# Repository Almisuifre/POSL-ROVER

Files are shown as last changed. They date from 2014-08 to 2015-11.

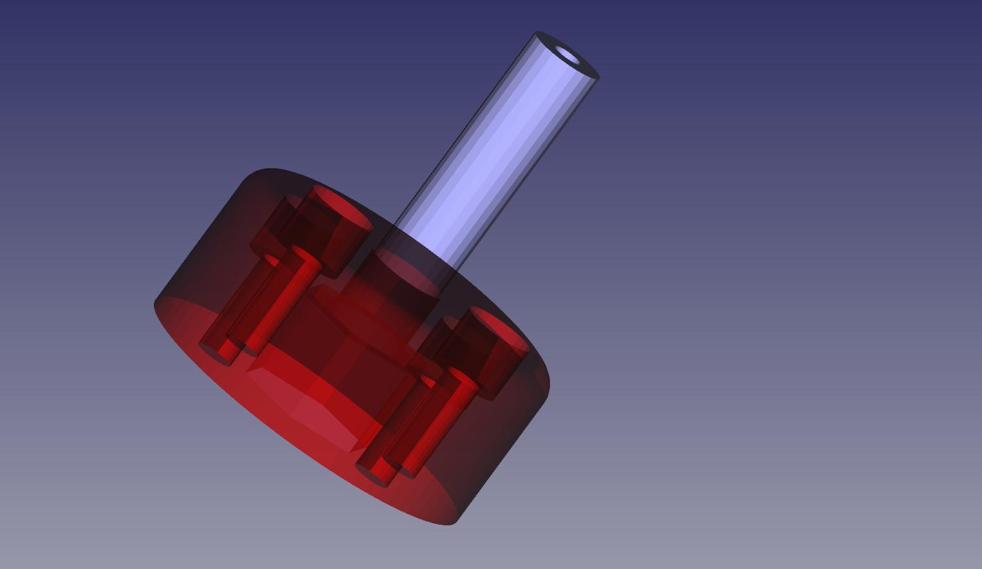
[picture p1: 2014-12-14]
Images/Assemblage-Chapot-pivot-et-pivot-axe.jpeg

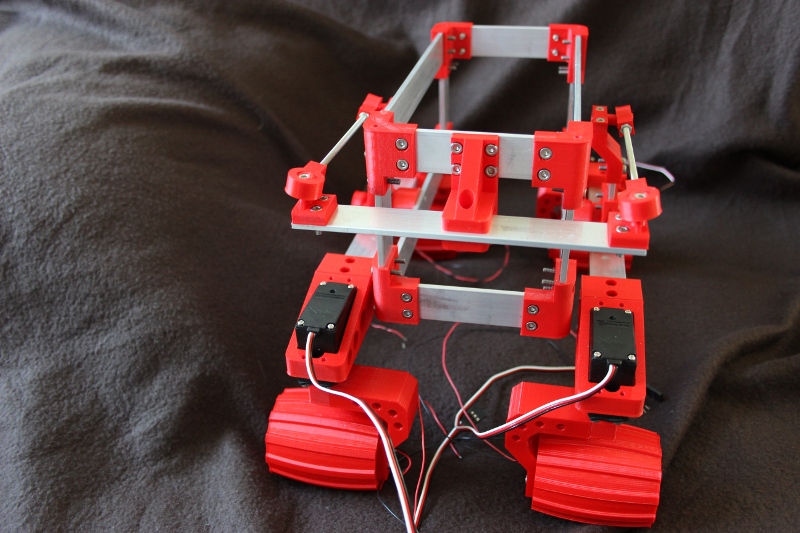
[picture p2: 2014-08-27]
Galerie/Montage-1/Img_002.jpg

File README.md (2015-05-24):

POSL

INFORMATIONS GENERALES
-----------------------------------------------------
-POSL est l'acronyme de Projet Open Source et Libre.

-L'ensemble du projet repose entièrement sur des logiciels Open Source et son hébergement est sous GitHub.

-----------------------------------------------------

LICENCE
-----------------------------------------------------
POSL Rover de Almisuifre est mis à disposition selon les termes de la licence Creative Commons Attribution - Partage dans les Mêmes Conditions 4.0 International.
Fondé(e) sur une œuvre à https://github.com/Almisuifre/POSL-ROVER.

<br /><span xmlns:dct="http://purl.org/dc/terms/" href="http://purl.org/dc/dcmitype/Dataset" property="dct:title" rel="dct:type">POSL Rover</span> de <span xmlns:cc="http://creativecommons.org/ns#" property="cc:attributionName">Almisuifre</span> est mis à disposition selon les termes de la <a rel="license" href="http://creativecommons.org/licenses/by-sa/4.0/">licence Creative Commons Attribution -  Partage dans les Mêmes Conditions 4.0 International</a>.<br />Fondé(e) sur une œuvre à <a xmlns:dct="http://purl.org/dc/terms/" href="https://github.com/Almisuifre/POSL-ROVER" rel="dct:source">https://github.com/Almisuifre/POSL-ROVER</a>.

-----------------------------------------------------

LOGICIELS EMPLOYES
-----------------------------------------------------
-FreeCad
-Cura
-MyPaint
-Git
-LibreOffice

-----------------------------------------------------

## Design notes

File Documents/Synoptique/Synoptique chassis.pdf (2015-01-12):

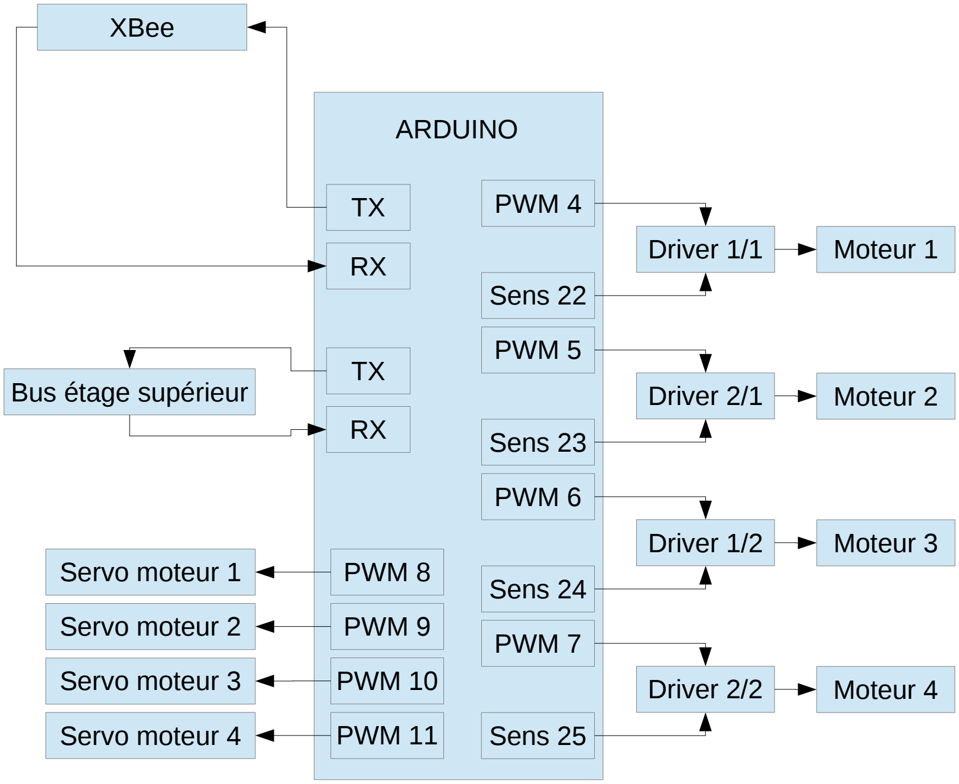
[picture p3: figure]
Moteur 1; Servo moteur 1; Servo moteur 2; Servo moteur 3; Servo moteur 4; PWM 8; PWM 9; PWM 10; PWM 11; PWM 4; Sens 22; Driver 1/1; Moteur 2; PWM 5; Sens 23; Driver 2/1; Moteur 3; PWM 6; Sens 24; Driver 1/2; Moteur 4; PWM 7; Sens 25; Driver 2/2; XBee; ARDUINO; Bus étage supérieur

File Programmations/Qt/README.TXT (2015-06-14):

Programmation C++
-----------------------------------------------------

Utilisation de Cute 5.4 32 bits

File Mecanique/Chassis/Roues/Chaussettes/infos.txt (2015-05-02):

*****************************
*	INFORMATIONS IMPORTANTES
***********************************

Les chaussettes sont à imprimer en Ninjaflex.
Elle s'installe par dessus la roue déjà créé.
Il n'en faut qu'une par roue.

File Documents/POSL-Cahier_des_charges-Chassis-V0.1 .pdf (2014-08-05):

# POSL

# Projet Open Source et Libre

# Châssis Robotique

# POSL-ROVER

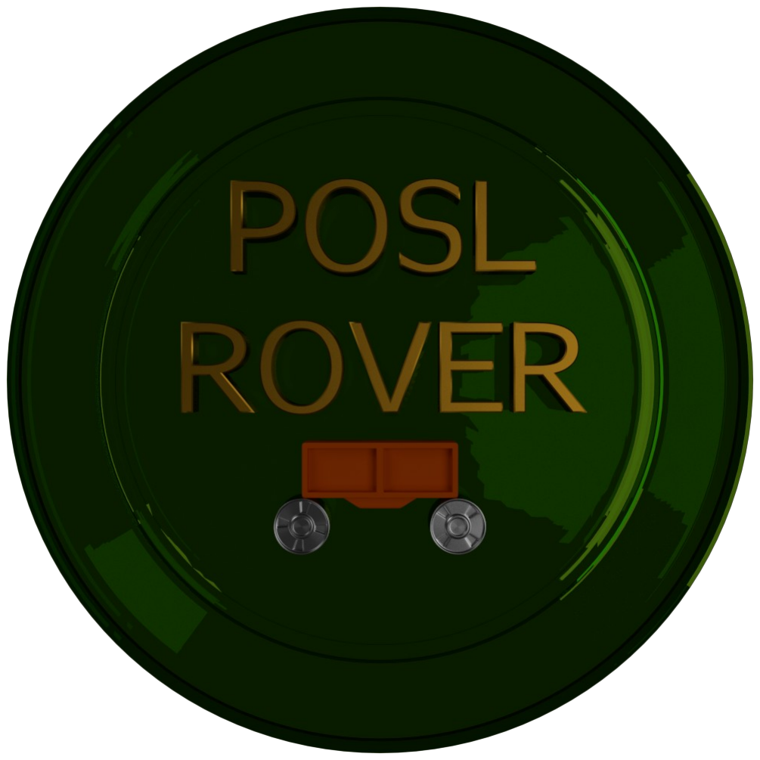
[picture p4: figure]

## Table des matières

## 1/ Genèse du concept

C'est au cours des diverses discussions et l'envie de promouvoir les réalisations libres et open sources qu'à émergée l'idée de créer un châssis robotique.
Une constatation : « La robotique c'est bien simple mais il faut un châssis » ! C'est souvent le point de départ des projets plus complexes et novateurs.
C'est en voulant allier conception libre et créativité autour d'un même projet que ce concept est née.

## 2/ Le but du projet

Le but de ce projet est de promouvoir, vous l'aurez compris, le monde du libre, la conception sur logiciel libre et la réalisation qui se voudra tout autant libre. Il convient de comprendre aussi que le but final n'est pas de s'arrêter là mais de disposer d'une base solide pour des développements en groupe autour de la robotique.

## 3/ Le POSL

Le POSL où bien Projet Open Source et Libre est un concept qui se veut le plus ouvert possible. C'est la définition d'une conception écrite, modélisé, inscrite dans le monde du libre et libre de diffusion. L'intégralité d'un Projet POSL doit être bâti avec des logiciels et des machines libre d'utilisation et open source (Voir le paragraphe 5).

## 4/ Châssis robotique

Un châssis robotique peut être à chenille, à roue, à pied ou tout autre moyen permettant le déplacement en milieu naturel comme en intérieur de maison habité.
Le châssis robotique doit de lui-même correspondre à une attente ferme du cahier des charge et doit être capable d'embarqué sans ajout tout les équipements nécessaire à son déplacement. Cela laisse totalement libre les parties restantes pour y placer des équipements d'étude scientifique ou des modules d'essais.

4.1/ Cahier des charges
Tout projet passe par un cahier des charge minimal. Il regroupe toute les spécificités nécessaire au bon fonctionnement du projet.

4.1.1/ Les impératifs généraux
- Un châssis qui a de la patate (qui ne craint pas de porter du poids et de monter une côte)
- Un châssis qui a de l'autonomie (plusieurs heures de fonctionnement à pleine charge)
- Un châssis tout terrain (Possibilité de fonctionner dans un jardin boueux)
- Un châssis ou il y a de la place pour les modules électronique, passage de câble…
- Un châssis Open Source et Libre
- Pas de panneaux pleins (limitation des ressources, allègement du matériel)
- Un maximum de récupération.
- Un coût dérisoire (Le plus faible possible, moins de 150€ pour la mécanique). Il est possible toutefois d'utiliser du matériel du commerce (servomoteur, platine électronique...)
- Plastique imprimé et Aluminium
- De la visserie M3 à 6 pans creux

4.1.2/ Les dimensions
Le châssis devant être facilement transportable, l'idée est de commencer petit. La surface doit être égale ou plus petite à la surface d'une feuille A4 21x29.7, la hauteur est laisser libre. Néanmoins, comme il sera question d'intégrer un plateau de développement, il ne devrais pas excéder 100mm (10cm) de haut.

4.1.3/ Plateau de développement
Sur le châssis, il faudra prévoir des points de fixation de tel sorte que d'autres équipements pourront y prendre place.
Le châssis comprend uniquement ses roues, ses moteurs, une batterie pour la propulsion, un module permettant le pilotage des moteurs, une carte électronique dédié au pilotage du châssis.
Au dessus de cet équipement de base, il y a le plateau. Au dessus du plateau, c'est laisser libre à des développements futurs.

## 5/ Logiciels - Workflow

L'exploitation de logiciels libre est nécessaire pour ce projet. Il est proposé d'utiliser des logiciels de CAO et DAO tel que FreeCad, LibreCad ou Blender. Il existe d'autres logiciels libre et open source.
À titre d'exemple, ma chaîne de production emploie divers logiciels et dans des domaines variés (voir le tableau ci-dessous). Vous pouvez, utiliser les mêmes logiciels et / ou utiliser votre propre chaîne de logiciel tant que ceux employé soit disponible sous Linux et q'ils soient Open Source ou Libre.
Domaine | Nom Logiciel | Licence
OS (Opérating System) | Debian | GNU Linux
| Ubuntu | GNU GPL
Ecriture / Documents | LibreOffice | LGPLv3
| Scribus (PAO) | GNU GPL
Art / Dessin | Gimp | GPLv3
| Inkscape | GNU GPL
3D / Animation | Blender | GNU GPLv3
Mecanique CAO | FreeCad | LGPL
Dessin CAO | LibreCad | GNU GPL
Musique MAO | LMMS | GNU GPL

## 6/ Mise à disposition des sources

Chacun peut utiliser son moyen de stockage de donnée local voulue. Néanmoins, il sera intéressant de regrouper chaque projet dans une section approprié.
En ce qui concerne mes dépôts, basé sur BITBUCKET, vous trouverez l'intégralité des fichiers créés sous cette adresse : https://bitbucket.org/posl/posl-rover/src . Il vous sera possible de « suivre » et ou de reprendre un fichier, comme l'intégralité du projet du moment que vous citez la source (l'adresse internet donné au dessus) ou bien le nom du projet.

## 7/ Matériel (Mécanique, Electronique, Matériaux)

La conception doit être reproduisible facilement. Dans cet optique, il est important de se baser le plus possible sur des composants et matériaux du commerce.
Toutes les références des composants peuvent être commandé via internet auprès de revendeurs agrée. Nous nous éfforcerons, dans le cadre de la réalisation des projet à citer les sources d'achats, les références ou nom des matériels. Cela vaut pour toute la mécanique, l'électronique et l'approvisionnement en matériaux.
Exemple concret. L'emploie de servomoteurs à fort couple pour la direction sera confié à des servos standard ayant des roulements à billes afin d'alléger le plus posible la contrainte de frottement. Dans la gamme des servo-moteurs le choix c'est porté sur des S3004 de marque Futaba. Il est possible d'avoir la taille de ce composant ainsi que les équivalences pour gérer au mieux vos projets.

## 8/ Durée de réalisation

À l'horison 2015, Janvier, il serait intéressant de faire un point sur la création. Néanmoins, les premiers tours de roues devront être réalisés entre Août 2014 et Janvier 2015, date de fin de phase 1.

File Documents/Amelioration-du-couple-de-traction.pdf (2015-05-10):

# POSL ROVER

## Amélioration du couple de traction par l'utilisation d'un train épicycloïdal

# Impression 3D

# PLA/PHA

POSL Rover : Amélioration de traction par l'utilisation d'un train épicycloïdal.

Almisuifre | Page 1 / 9

Présentation

Lors de l'utilisation du POSL-Rover avec des moteurs-réducteurs (moto-réducteurs) POLOLU de rapport de réduction 298:1, alimenté sous 6V, je m'étais rendu compte de la trop grande rapidité et de la perte de couple importante de ce système.

L'idée première est donc de réduire considérablement la vitesse de rotation imprimée à chacune des roues afin d'en augmenter le couple. Je ne voulais pas changer, pour des raisons évidentes de conception : les moteurs, les roues et l'empattement de l'ensemble du mécanisme. La solution retenu est le train épicycloïdal car elle a démontré son efficacité dans des systèmes connus et utilisé tous les jours (voiture, char, industrie lourde).

Le train épicycloïdal est un système planétaire composé d'un pignon central, d'un ou plusieurs pignons satellites entraînant une couronne centrale et qui est englobé dans une couronne dentée.

On considère que le moteur est fixé sur la couronne dentée externe. Par ce principe, lorsque la roue dentée du centre (soleil) est entraînée par le moteur, elle entraîne à son tour les roues dentées (satellites). Le fait que les satellites sont en rotation autour de la roue dentée externe, ils entraînent. la couronne centrale. Cela provoque une démultiplication importante.

En outre, il est possible de mettre plusieurs trains planétaires à la suite, en étage. Le rapport de réduction en est d'autant augmenté. Dans notre cas, il est évident que la place manquerait si l'on optait pour un tel système. Alors, un seul train planétaire sera utilisé.

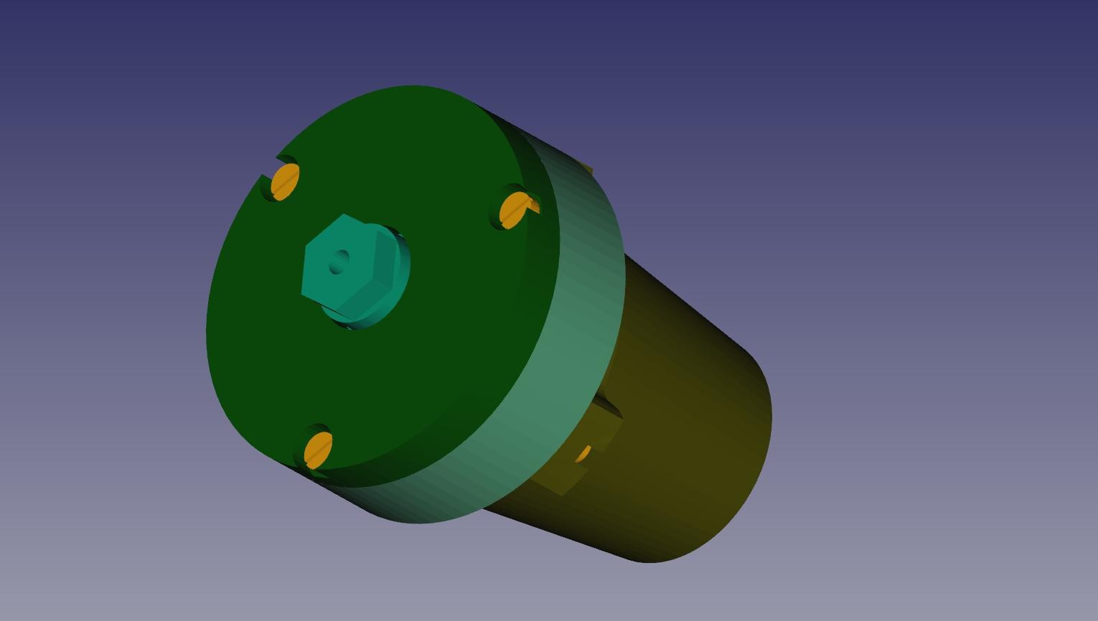
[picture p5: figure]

POSL Rover : Amélioration de traction par l'utilisation d'un train épicycloïdal.

Almisuifre | Page 2 / 9

Modélisation

La modélisation à été effectuée sous FreeCad. Le but étant de rester sous logiciel open source et de montrer que c'était finalement réalisable.

Dans un soucis de simplicité, je n'ai pas mis de développante de cercle sur les dents des engrenages. Il est cependant envisageable à terme de les ajouter afin de gagner en souplesse et en bruit.

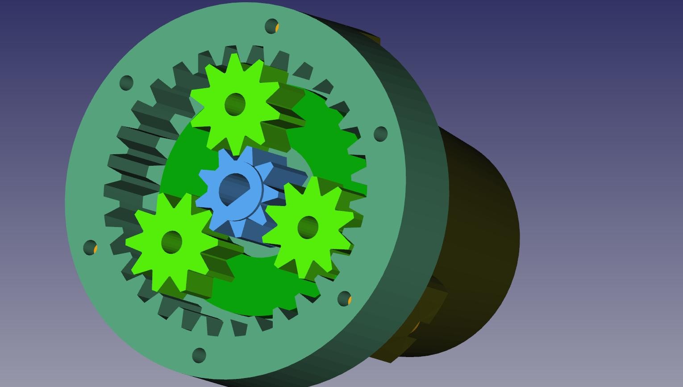
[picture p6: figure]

Dans cette image, on voit parfaitement la couronne centrale (vert) sous les engrenages planétaires (vert clair) et aussi l'engrenage d'entraînement (bleu), le soleil, au centre.

De nombreuses heures ont été nécessaires pour calculer les cercles primaires, le module utilisé et enfin le report sur le dessin 3D. En effet, j'ai procédé par tests successifs afin d'avoir le meilleur compromis.

Dans un but didactique, je vous donne quelques liens qui m'ont été très utiles.

http://archivemiq.free.fr/archives/archives_S3/CE2/Cours/Train%20%C3%A9picycloidal.pdfhttp://www.scd.uhp-nancy.fr/docnum/SCD_T_2011_0024_GOUDA.pdfhttp://www.raymondn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

Le train épicycloïdal est régi par la relation de WILIS (on peut retrouver celle-ci en cherchant sous Google).

POSL Rover : Amélioration de traction par l'utilisation d'un train épicycloïdal.

Almisuifre | Page 3 / 9

Pour commencer, je suis parti de l'engrenage central. Il possède donc un module « m » de 0.8 et il est normalisé. J'ai pu ainsi utiliser le pas « p » qui est utilisable par la relation p = П.m. Avec la tangente du cercle primitif et de p/2, on obtient la taille de la denture en son centre. Une pente de 20° est donnée à la dent afin qu'elle puisse se dégager sans forcer. Et enfin, la auteur du pied de la dent est de m.1,25 à partir du cercle primitif.

Pour mieux comprendre comment dessiner la dent droite, je vous propose de visionner la page 298 du livre « Chevalier : Guide du dessinateur industriel / édition 2004 : Hachette Technique ». Vous y retrouverez toute la normalisation et les données que j'ai exploité afin de réaliser ces engrenages.

Le même système de relation à été utilisé pour dessiner les planétaires et la couronne externe.

Montage du nouvel ensemble : étape par étape

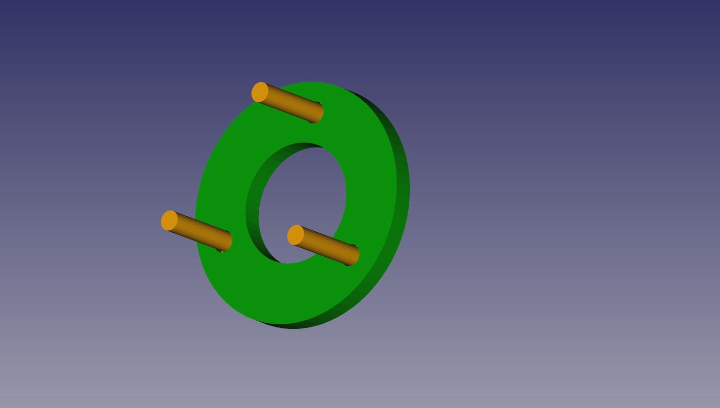
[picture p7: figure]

Première étape, mettre 3vis M2 de 10mm sous tête dans la couronne planétaire.

POSL Rover : Amélioration de traction par l'utilisation d'un train épicycloïdal.

Almisuifre | Page 4 / 9

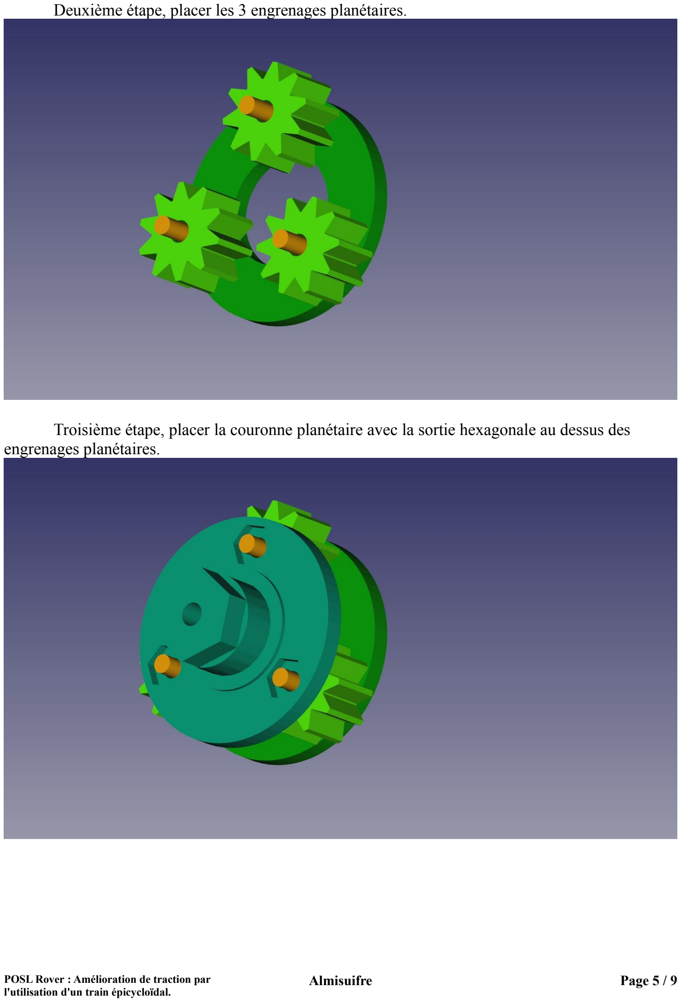
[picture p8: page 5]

Deuxième étape, placer les 3 engrenages planétaires.

Troisième étape, placer la couronne planétaire avec la sortie hexagonale au dessus des engrenages planétaires.

POSL Rover : Amélioration de traction par l'utilisation d'un train épicycloïdal.

Almisuifre | Page 5 / 9

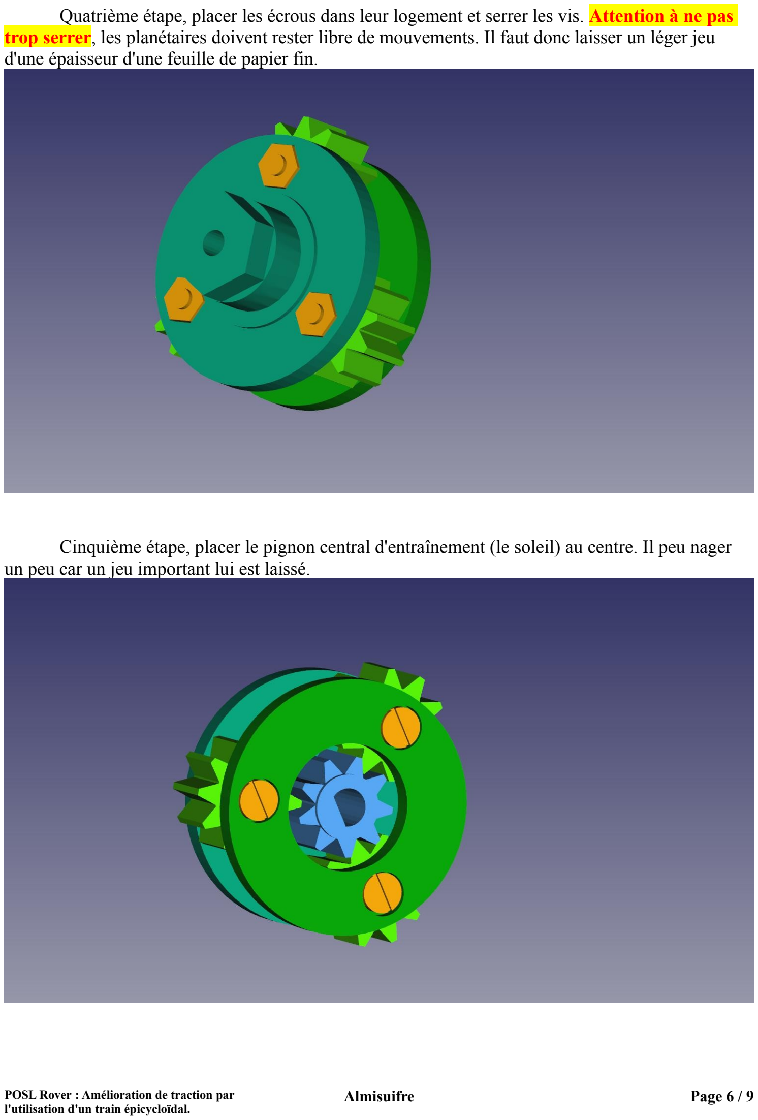
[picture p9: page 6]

Quatrième étape, placer les écrous dans leur logement et serrer les vis. Attention à ne pas trop serrer, les planétaires doivent rester libre de mouvements. Il faut donc laisser un léger jeu d'une épaisseur d'une feuille de papier fin.

Cinquième étape, placer le pignon central d'entraînement (le soleil) au centre. Il peu nager un peu car un jeu important lui est laissé.

POSL Rover : Amélioration de traction par l'utilisation d'un train épicycloïdal.

Almisuifre | Page 6 / 9

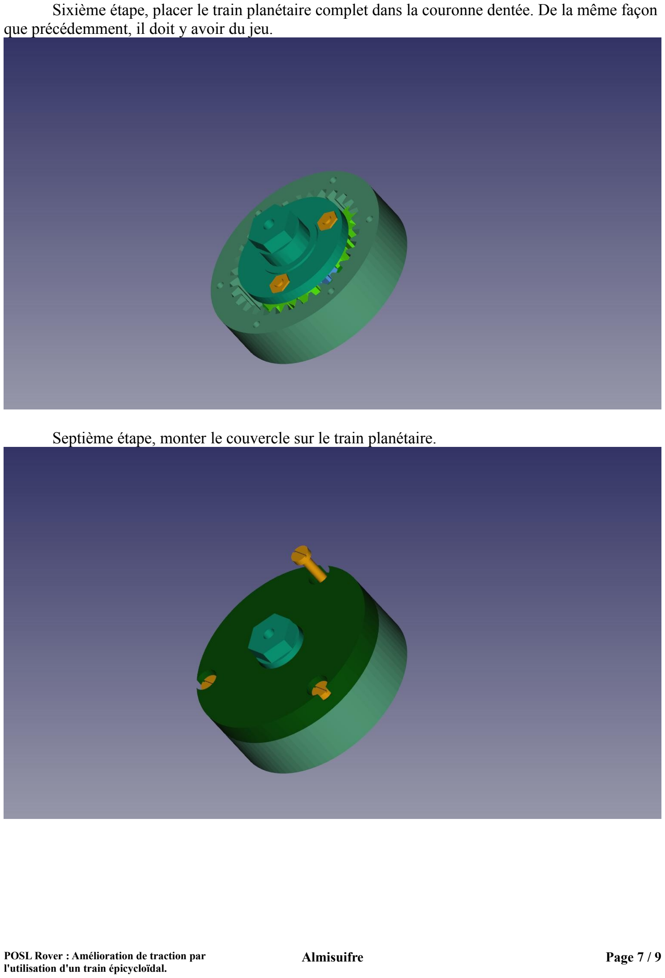
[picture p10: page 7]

Sixième étape, placer le train planétaire complet dans la couronne dentée. De la même façon que précédemment, il doit y avoir du jeu.

Septième étape, monter le couvercle sur le train planétaire.

POSL Rover : Amélioration de traction par l'utilisation d'un train épicycloïdal.

Almisuifre | Page 7 / 9

Huitième étape, viser le couvercle sur la couronne externe. Vous pouvez maintenant faire tourner la partie hexagonale et voir que l'engrenage central va plus vite. C'est normal, car on utilise le réducteur en sens inverse de son utilité. Toutefois cette méthode montre que l'ensemble fonctionne sans trop se gripper.

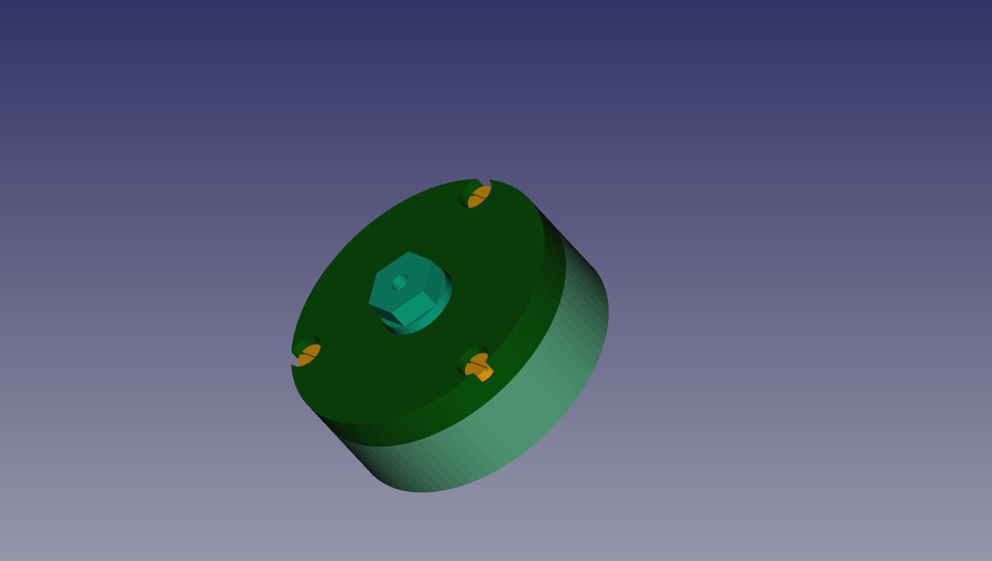
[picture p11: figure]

Neuvième étape, Insérer le moteur sur le pignon central, puis positionner le flasque moteur. C'est ce flasque qui assure le positionnement ferme du moteur et son réducteur intégré ainsi que sa protection à la projection de poussières. Pensez, avant de fermer à placer les fils électrique qui permettront de piloter le moteur-réducteur.

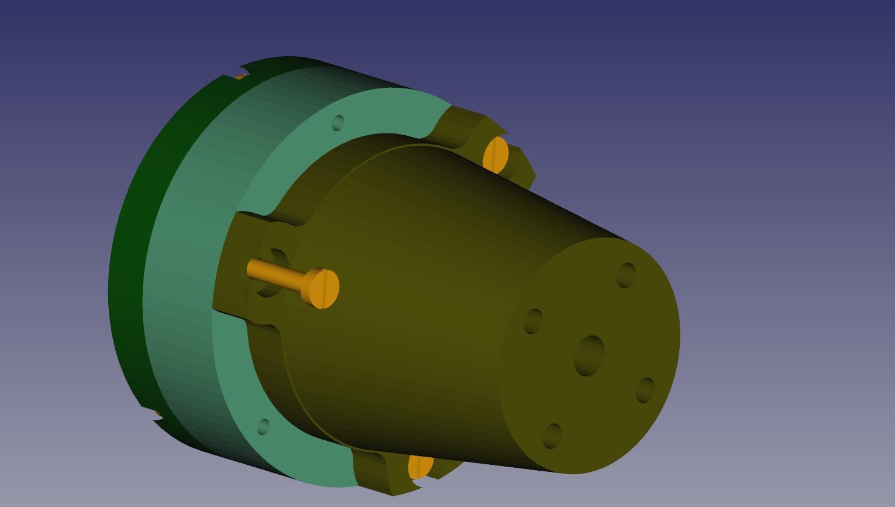
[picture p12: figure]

POSL Rover : Amélioration de traction par l'utilisation d'un train épicycloïdal.

Almisuifre | Page 8 / 9

Dixième étape, viser le flasque sur la couronne dentée externe.

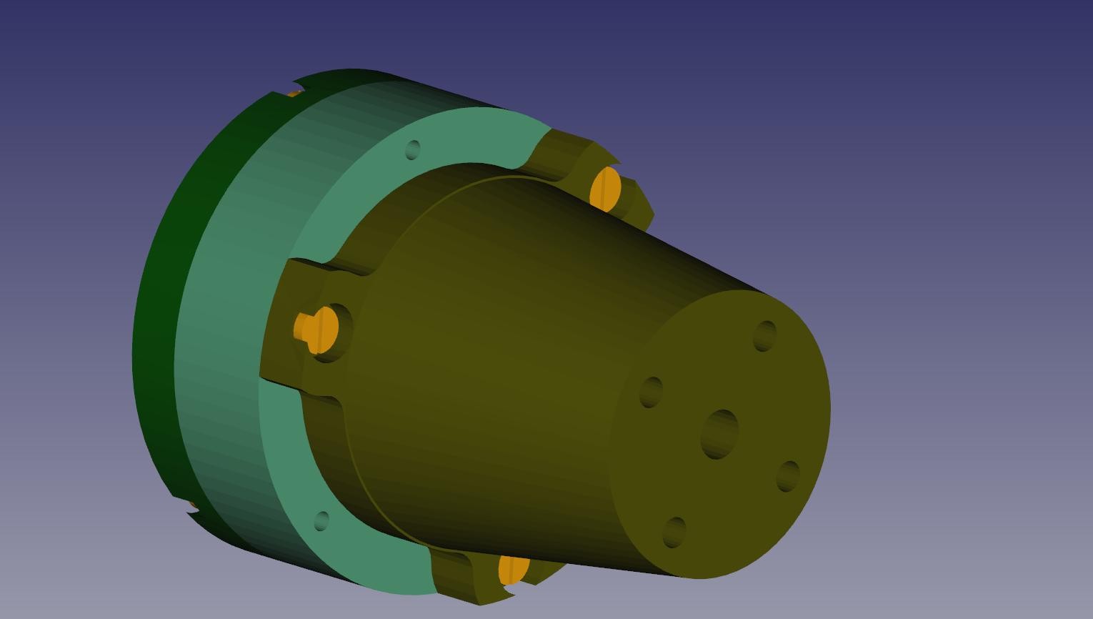
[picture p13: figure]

Conclusions
Le moteur-réducteur avec train planétaire est maintenant monté, il n'y as plus qu'à y mettre une tension de 3 à 6V pour le commander.

Vous remarquerez que la vitesse de sortie est plus lente et qu'il est presque impossible de bloquer la rotation avec les mains. Alors nous avons bien réduit la vitesse de rotation tout en augmentant le couple de façon importante.

Remerciements
Je remercie mes amis, Yo, Hardman, Juju, Artspy, Michelou de m'avoir aidé et soutenu dans la démarche de cet option.

Je remercie également les auteurs des ouvrages cités qui m'ont permis de comprendre le fonctionnement du train épicycloïdal et son emploi.

POSL Rover : Amélioration de traction par l'utilisation d'un train épicycloïdal.

Almisuifre | Page 9 / 9

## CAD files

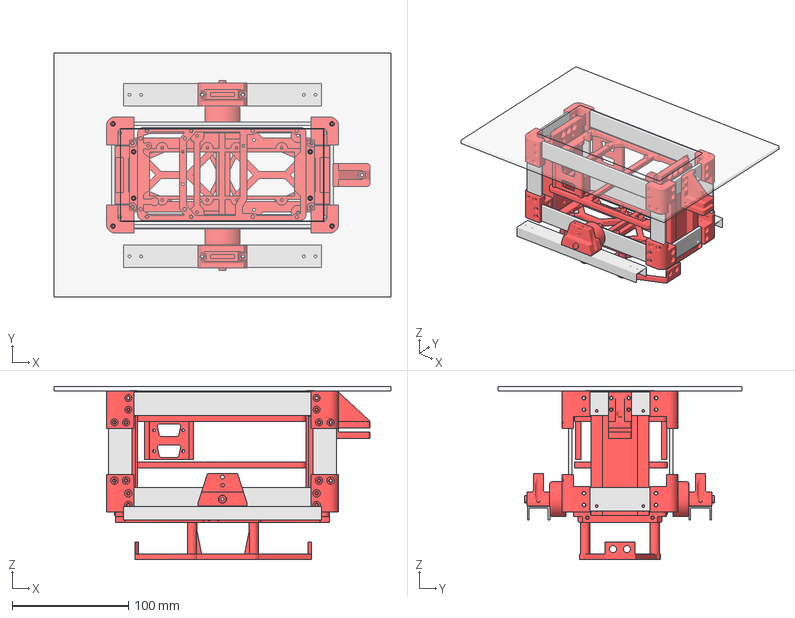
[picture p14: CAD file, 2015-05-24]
Mecanique/Assemblage_01.fcstd
290.0 x 210.0 x 149.0 mm
Plat_Type4
Plat_Type7
Plat_Type012
Plat_Type
Coin_Type2-B001
Coin_Type2-A002
Coin_Type2-A004
Coin_Type2-B003
Plat_Type3
Plat_Type2
Plat_Type007
Plat_Type013
Plat_Type009
Plat_Type010
Plat_Type014
Integ-Q-Arronde_A
Integ-Q-Arronde_A001
Support-Palonnier
Plat_Type6
Integ-Q-Arronde_B_V3
Integ-Q-Arronde_B_V004
Plateau_AlimV3
Plateau_Arduino
Plateau_Drivers
Integ-Sub_D9-T1
Integ-Sub_D9-T002
Plateau_1
Plateau_2
Pivot-Axe
Pivot-Axe001
Chapeau-pivot
Chapeau-pivot001
Pivot-Renvoie
Pivot-Renvoie001
Bras-Suspension
Coin_Type4-A
Coin_Type4-A001
Coin_Type4-B
Coin_Type4-B001
Pannier_Batterie
Bras-Suspension001
Support_pannier_A
Support_pannier_A001
Support_pannier_B
Support_pannier_B001

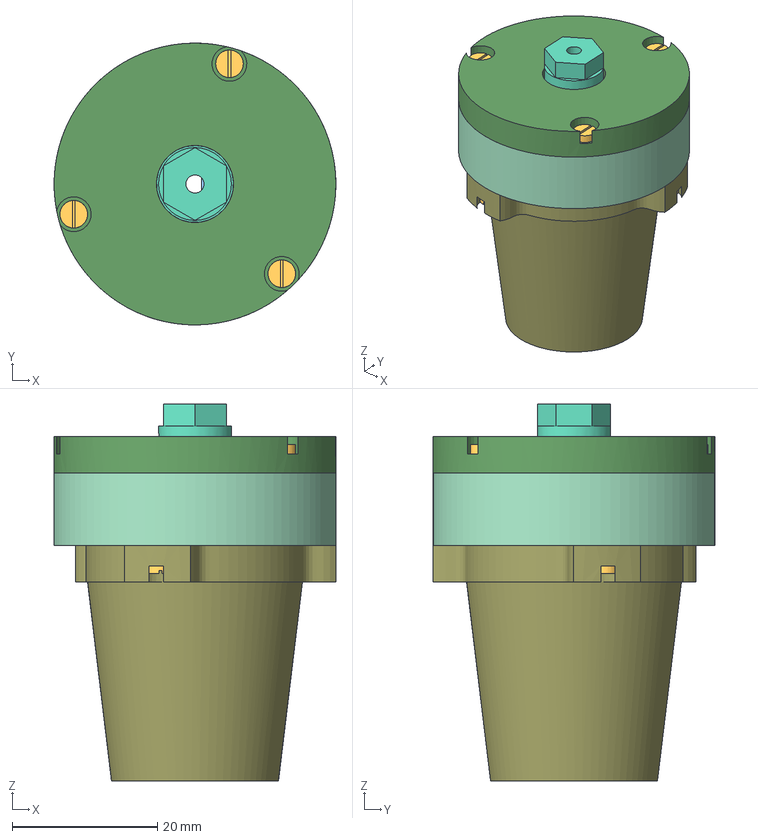
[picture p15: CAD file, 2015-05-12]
Mecanique/Chassis/Moteurs/Train-Epicycloidal/Assemblage.fcstd
38.8 x 38.8 x 51.9 mm
Courone_B
Ecrou-Laiton-M2
Vis-Laiton-ST_10-M2
Satellites
Ecrou-Laiton-M003
Vis-Laiton-ST_10-M003
Satellites001
Ecrou-Laiton-M004
Vis-Laiton-ST_10-M004
Satellites002
Courone-Ext_A
Soleil
Courone-Ext_B
Vis-Laiton-ST_10-M005
Vis-Laiton-ST_10-M006
Vis-Laiton-ST_10-M007
Flasque-Moteur
Vis-Laiton-ST_10-M008
Vis-Laiton-ST_10-M009
Vis-Laiton-ST_10-M010
Couronne_A_2

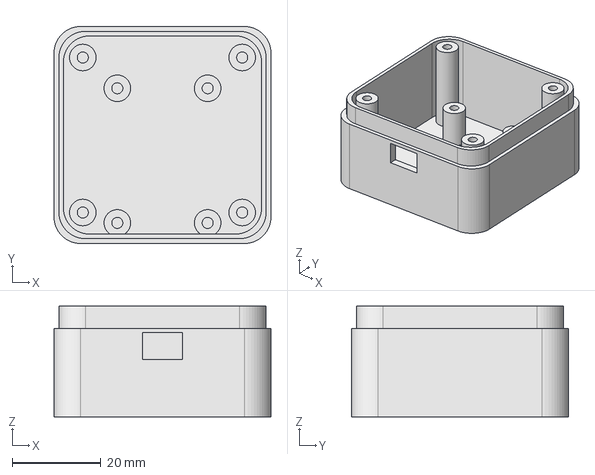
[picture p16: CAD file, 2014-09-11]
Mecanique/Boitier-Iface/Iface-Pc-Xbee-A.fcstd
49.0 x 49.0 x 25.0 mm

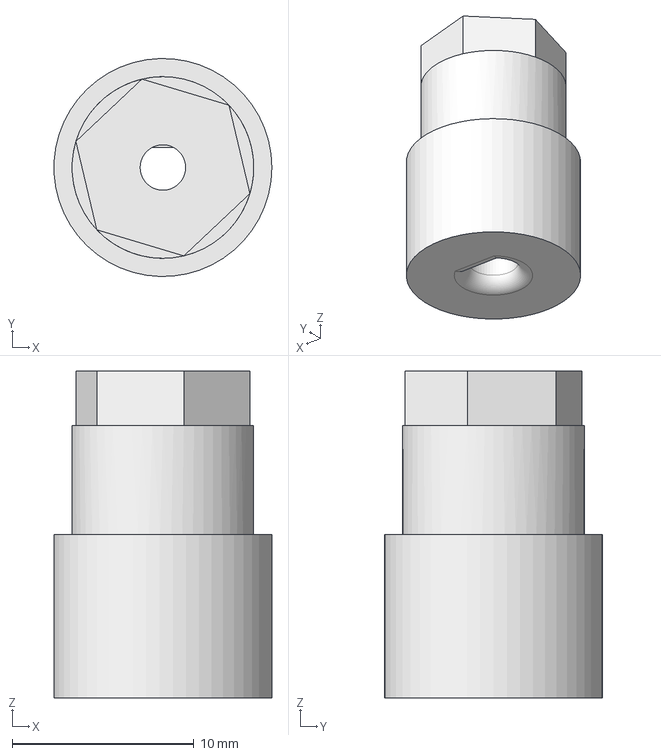
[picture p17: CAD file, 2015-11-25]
Mecanique/Chassis/Moteurs/Axe-Moteur-Roue/Axe_Moteur_Roue.step
12.0 x 12.0 x 18.0 mm

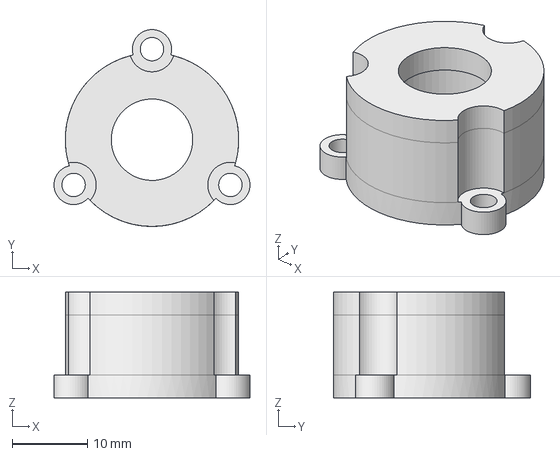
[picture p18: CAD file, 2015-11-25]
Mecanique/Chassis/Moteurs/Flasque-Moteur/Flasque_Moteur_B.step
26.0 x 26.1 x 14.0 mm

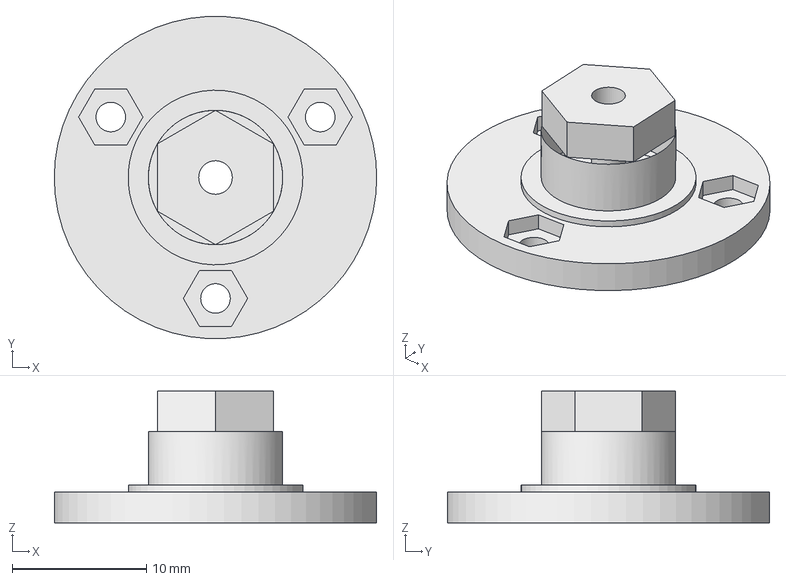
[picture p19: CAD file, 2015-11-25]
Mecanique/Chassis/Moteurs/Train-Epicycloidal/Couronne_B.step
24.0 x 24.0 x 9.80 mm

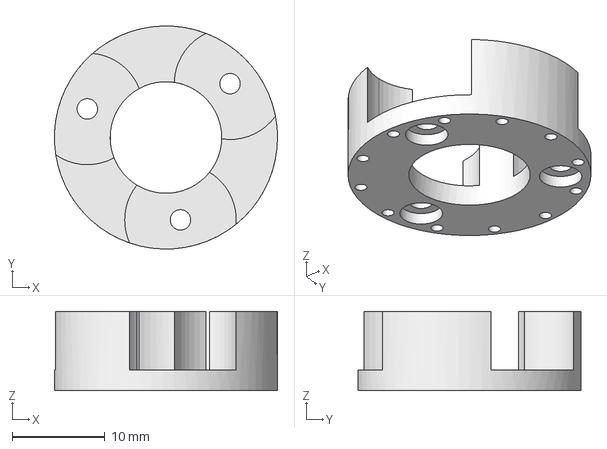
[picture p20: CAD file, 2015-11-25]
Mecanique/Chassis/Moteurs/Train-Epicycloidal/Odometrie/Odo-Couronne.fcstd
24.0 x 24.0 x 8.50 mm

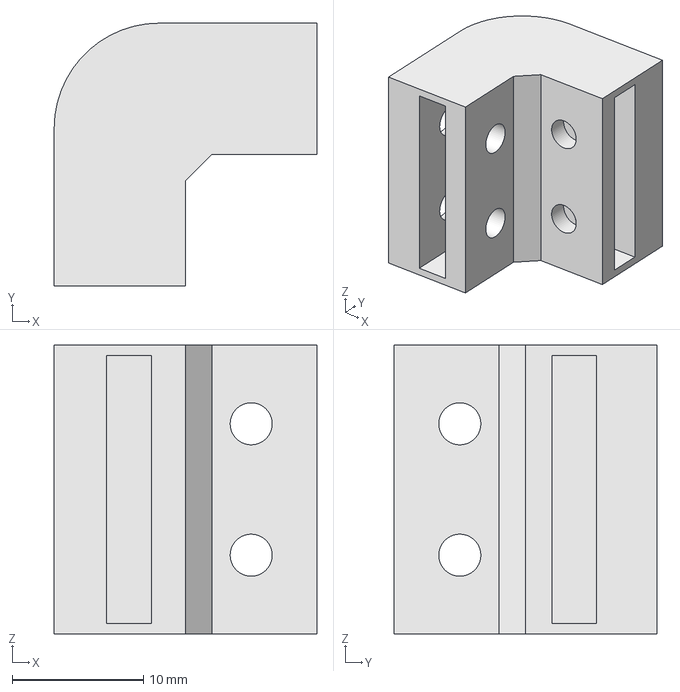
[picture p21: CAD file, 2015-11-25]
Mecanique/Chassis/Ossature/Coin_Type1.step
20.0 x 20.0 x 22.0 mm

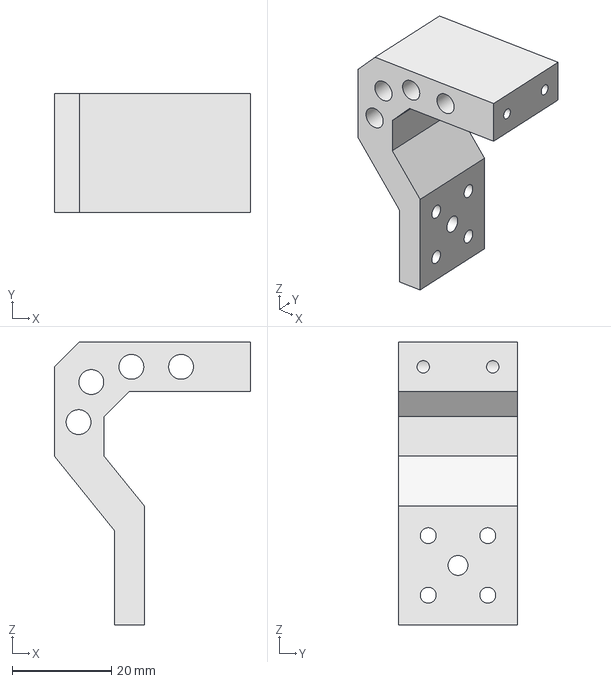
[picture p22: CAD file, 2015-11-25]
Mecanique/Chassis/Pivot/Pivot.step
39.5 x 24.0 x 57.0 mm

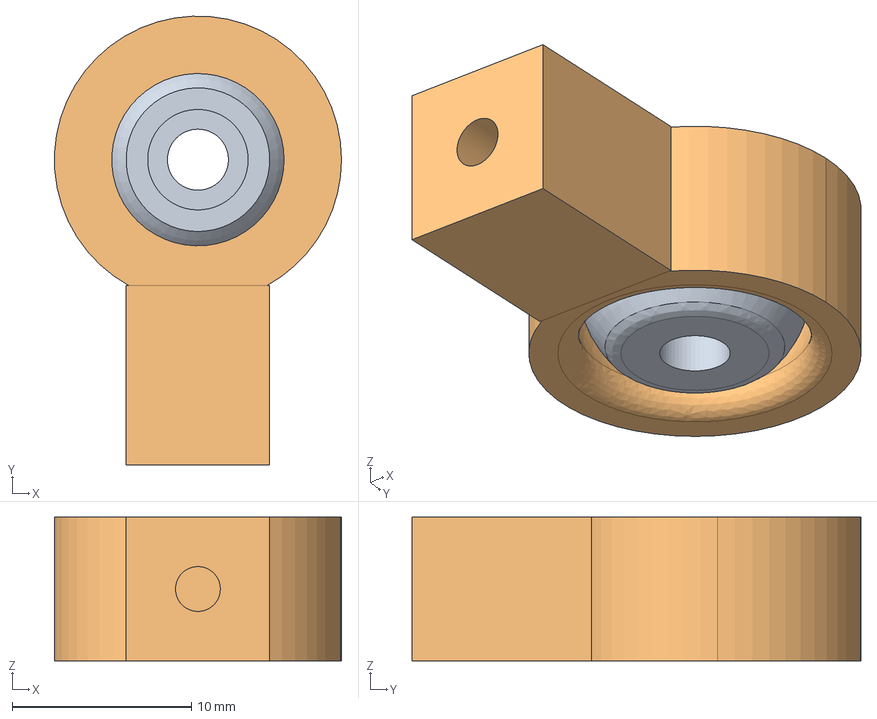
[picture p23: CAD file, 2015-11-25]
Mecanique/Chassis/Rotules/Rotule_Type1_Prussa.step
16.0 x 25.0 x 8.00 mm

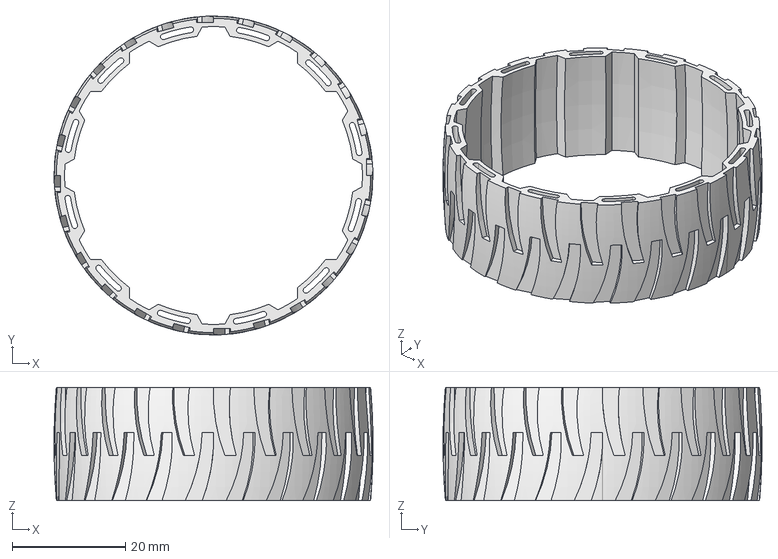
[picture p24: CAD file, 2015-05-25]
Mecanique/Chassis/Roues/Chaussettes/Chaussette-2.fcstd
56.2 x 56.2 x 20.0 mm

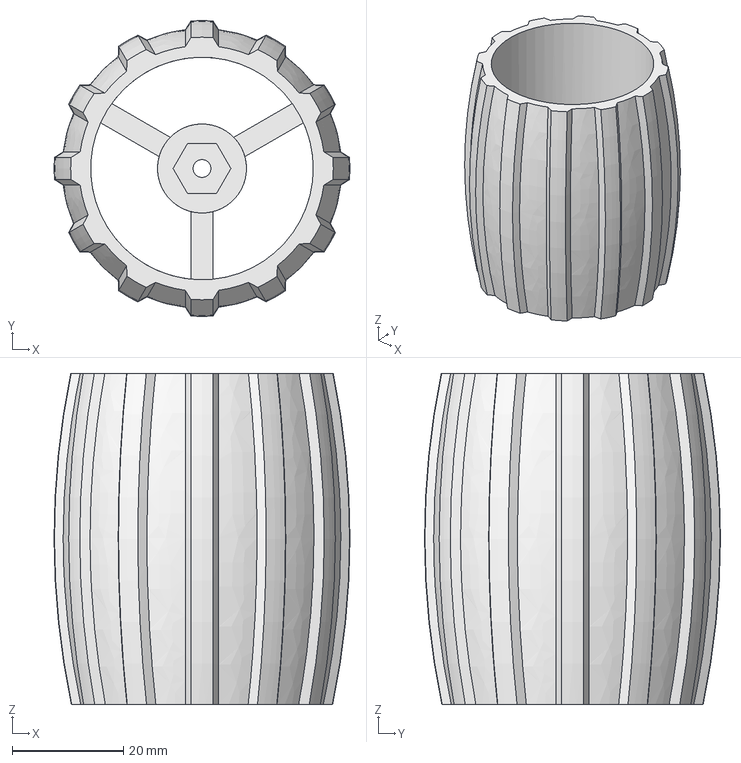
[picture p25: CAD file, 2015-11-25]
Mecanique/Chassis/Roues/Roue-Type1.step
53.2 x 53.2 x 59.5 mm

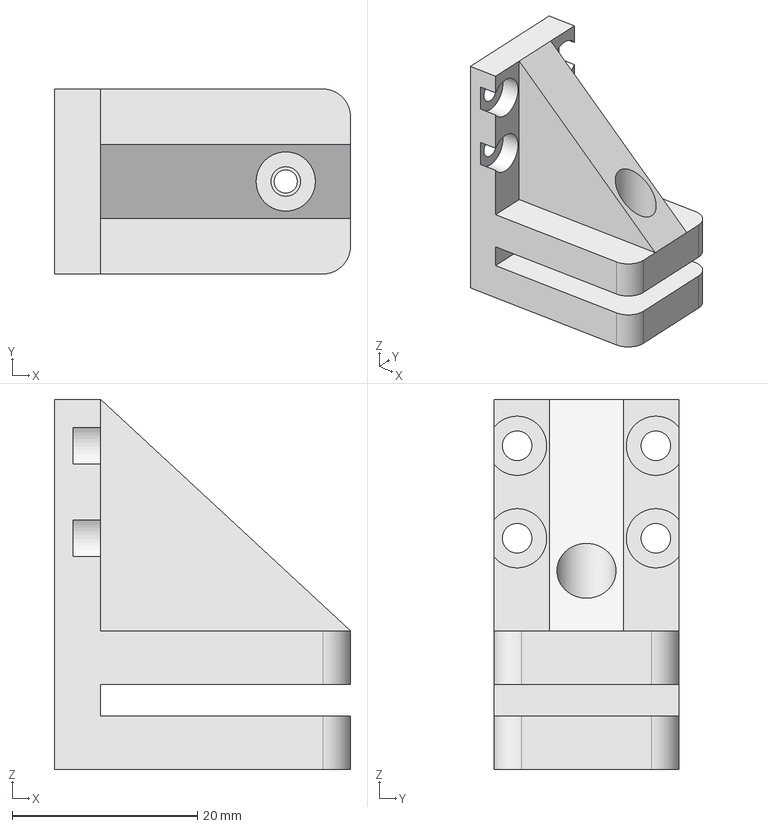
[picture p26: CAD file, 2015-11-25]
Mecanique/Chassis/Suspension/Support-Palonnier.step
32.0 x 20.0 x 40.0 mm

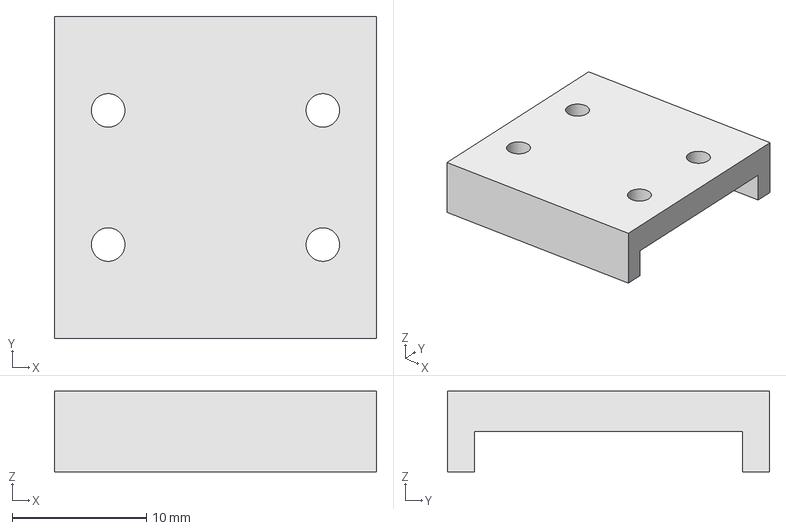
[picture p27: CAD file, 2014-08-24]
Mecanique/Gabarits/Gab-03.fcstd
24.0 x 24.0 x 6.00 mm

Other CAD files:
Mecanique/Integration/Batterie/Support_pannier_B.fcstd
Mecanique/Integration/Integ-Sub_D9-T3.fcstd
Mecanique/Pieces-Achetes/Boulon-M2/Vis-Laiton-ST_10-M2.fcstd
Mecanique/Pieces-Achetes/Plat-20x3/Plat_Type6.fcstd
Mecanique/Boitier-Iface/Iface-Pc-Xbee-A.stl
Mecanique/Boitier-Iface/Iface-Pc-Xbee-B.fcstd
Mecanique/Boitier-Iface/Iface-Pc-Xbee-B.stl
Mecanique/Chassis/Moteurs/Axe-Moteur-Roue/Axe_Moteur_Roue.fcstd
Mecanique/Chassis/Moteurs/Axe-Moteur-Roue/Axe_Moteur_Roue.stl
Mecanique/Chassis/Moteurs/Flasque-Moteur/Flasque_Moteur_A.fcstd
Mecanique/Chassis/Moteurs/Flasque-Moteur/Flasque_Moteur_A.step
Mecanique/Chassis/Moteurs/Flasque-Moteur/Flasque_Moteur_A.stl
Mecanique/Chassis/Moteurs/Flasque-Moteur/Flasque_Moteur_B.fcstd
Mecanique/Chassis/Moteurs/Flasque-Moteur/Flasque_Moteur_B.stl
Mecanique/Chassis/Moteurs/Train-Epicycloidal/Couronne-Ext_A.fcstd
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

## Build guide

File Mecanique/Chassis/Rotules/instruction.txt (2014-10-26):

Instruction pour imprimer le fichier Rotule_Type1_Prussa en couche de 0,1 sur prussa I3.

1/ La température doit être légèrement réduite. 215° initial (chez moi) -> 205°C 
2/ Le flow étant pas mauvais à 100% je le laisse à 100%
3/ La vitesse est de 20mm/s sauf pour le first layer qui lui est à 10mm/s
4/ Le plateau est fixé à 60°C (il peut y avoir de la rétractation en cours de route. Voir pour imprimé sur plus froids).
5/ La distance entre le plateau de verre et la buse est d'une feuille de papier + un quart de tours de clef sur vis M3 à pas e 0.5mm.

Pour la petite histoire, si ça peut rassuré, il faut jouer sur tous les paramètres et de surcroît faire de nombreux essais avant d'arrivé à un résultat correct. Cela à été aussi le cas de la première version qui elle demande plus de précisons sur X et Y.

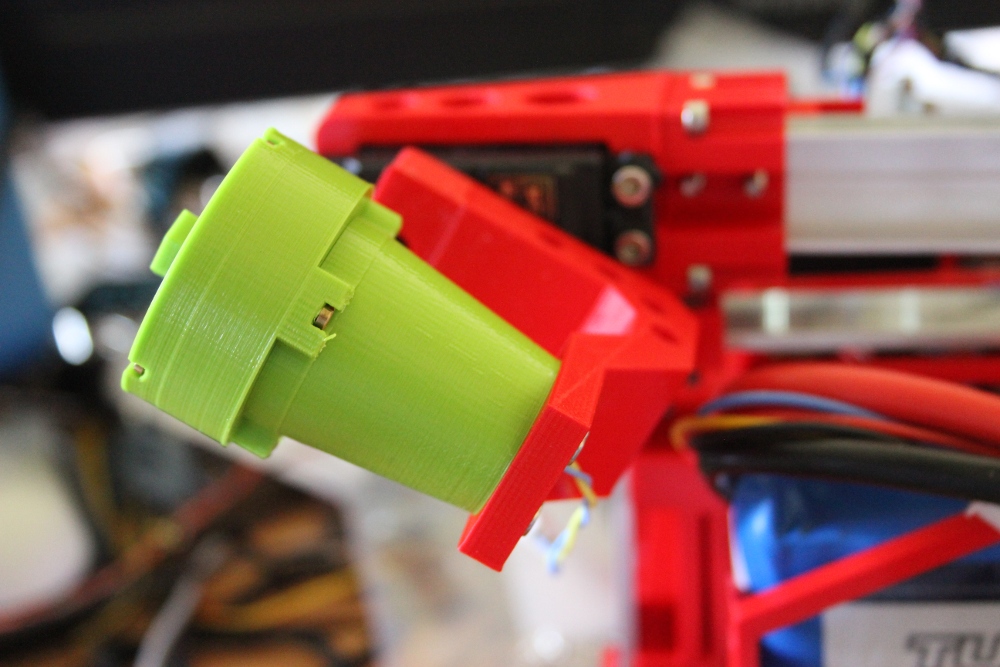
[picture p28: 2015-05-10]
Galerie/Train-Epicycloidal/Montage_11.JPG

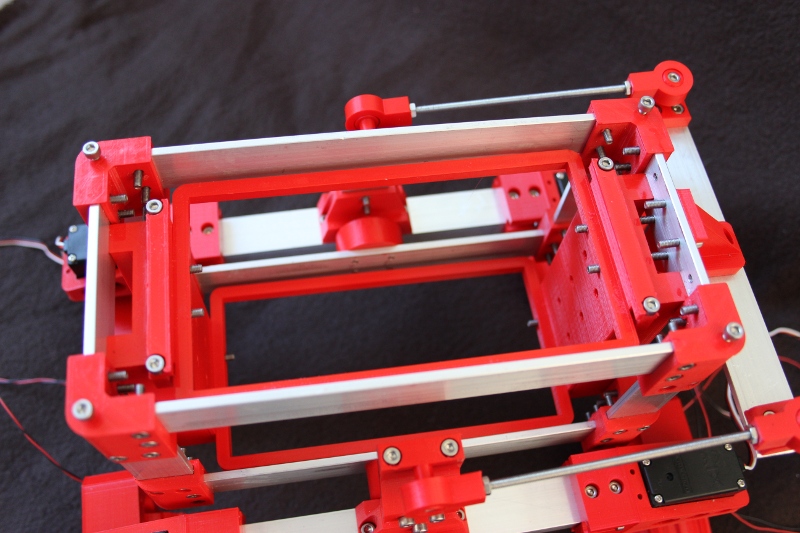
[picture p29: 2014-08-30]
Galerie/Montage-2/Img_002.jpg

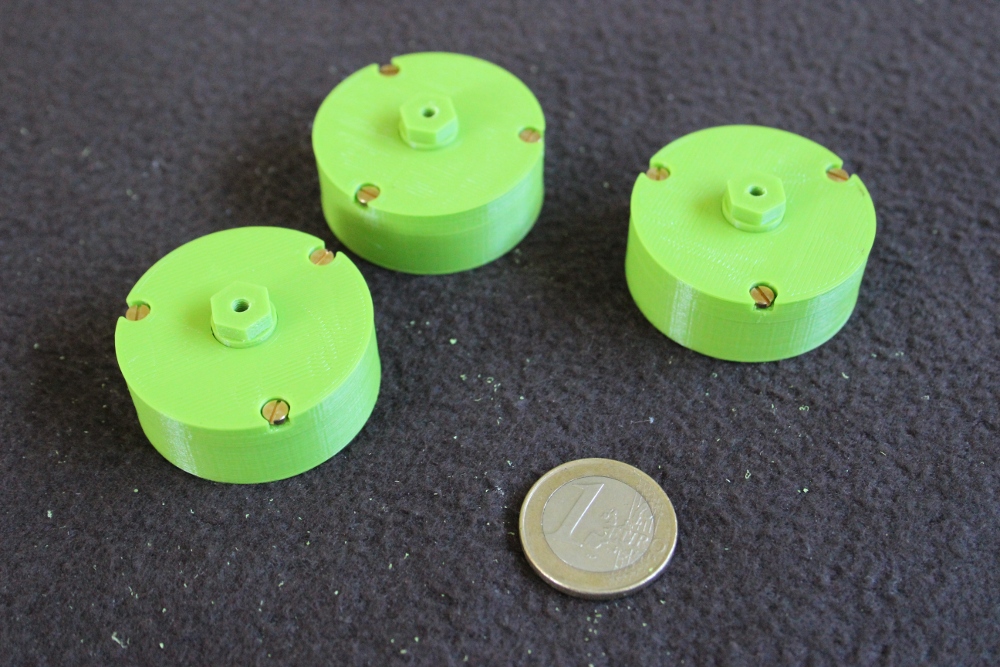
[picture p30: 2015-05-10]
Galerie/Train-Epicycloidal/Montage_07.JPG

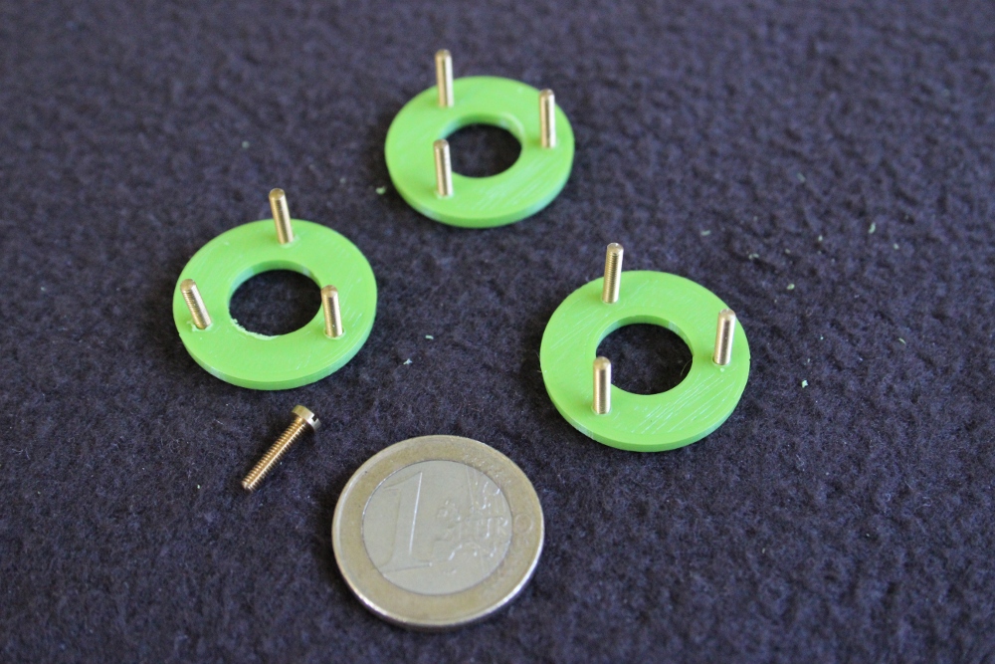
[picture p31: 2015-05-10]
Galerie/Train-Epicycloidal/Montage_01.JPG

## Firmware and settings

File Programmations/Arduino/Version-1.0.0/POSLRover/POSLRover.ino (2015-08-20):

/*
                    POSL Rover

    Debut de programmation 30/01/2015 Par Almisuifre
    Aide à la programmation Phil
    
    Les instructions sont basés sur le format CSV.
    Exemples (moteur):
          dir,vitesseAVG,dir,vitesseARG,dir,vitesseAVD,dir,vitesseARG
      !,1,0,0,0,0,0,0,0,0,* = STOP
      !,1,1,100,1,100,1,100,1,100,* = Moteurs Marche AV
      !,1,0,100,0,100,0,100,0,100,* = Moteurs Marche AR
      
    Exemples (Directions):
          AVG,ARG,AVD,ARD
      !,2,90,90,90,90,*  = Roues au centre
      !,2,70,110,70,110,*  = Roues permettant de tourner à gauche
      !,2,110,70,110,70,* = Roues permettant de tournet à droite
      !,2,70,70,70,70,*  = En diagonale gauche
      !,2,110,110,110,110,*  = En diagonale droite
      !,2,140,40,40,140,*  = Tourner sur place
      
*/

/* -- INCLUDES -- */
#include "Servo.h"
#include "Dri2.h"

/* -- DEFINE -- */
#define ServoAvG  2    //Servo (avant gauche) sur patte 2
#define ServoArG  3    //Servo (arrière gauche) sur patte 3
#define ServoAvD  4    //Servo (avant droit) sur patte 4
#define ServoArD  5    //Servo (arrière droit) sur patte 5

#define PWM_MAvG  6    //PWM sur sortie 6 (avant gauche) -> E1 Carte 1
#define SEN_MAvG  22   //Sens sur sortie 22 (avant gauche)  -> M1 Carte 1

#define PWM_MAvD  7    //PWM sur sortie 7 (avant gauche) -> E2 Carte 1
#define SEN_MAvD  24   //Sens sur sortie 24 (avant gauche)  -> M2 Carte 1

#define PWM_MArG  8    //PWM sur sortie 8 (arrière gauche) -> E1 Carte 2
#define SEN_MArG  23   //Sens sur sortie 23 (arrière gauche)  -> M1 Carte 2

#define PWM_MArD  9    //PWM sur sortie 9 (arrière gauche) -> E2 Carte 2
#define SEN_MArD  25   //Sens sur sortie 25 (arrière gauche)  -> M2 Carte 2

#define BUFFER_SIZE          11  // Taille du buffer de données  // basé sur ! , instruction(int) , 90 , 90 , 90 , 90 , 90, 90, 90, 90, *
#define START_CHAR           '!' // caractere de début
#define STOP_CHAR            '*' // caractere de fin
#define SEP_CHAR             ',' // caractere de séparation
#define INSTRUCTION_MOTEURS  1   // instruction moteur
#define INSTRUCTION_DIR      2   // instruction direction

#define SERVO_CENTRE_AVG  88
#define SERVO_CENTRE_ARG  94
#define SERVO_CENTRE_AVD  96
#define SERVO_CENTRE_ARD  92

/* -- INSTANCIATIONS -- */
Servo ServoAvantGauche;  //Servomoteur avant gauche
Servo ServoArrieGauche;  //Servomoteur arriere gauche

Servo ServoAvantDroit;  //Servomoteur avant droit
Servo ServoArrieDroit;  //Servomoteur arriere droit

Dri2 MoteurAvantGauche(SEN_MAvG, PWM_MAvG);
Dri2 MoteurAvantDroit(SEN_MAvD, PWM_MAvD);
Dri2 MoteurArriereGauche(SEN_MArG, PWM_MArG);
Dri2 MoteurArriereDroit(SEN_MArD, PWM_MArD);

/* -- VARIABLES -- */
char  buffer[BUFFER_SIZE];                  // String buffer 
boolean transmissionTerminee = false; // Boolean qui indique que la transmission est terminée
int index = 0;
char a;

String inputString = "";         // a string to hold incoming data
boolean stringComplete = false;  // whether the string is complete

/* -- SETUP -- */
void setup() {
  
  //Connexion série
  Serial.begin(9600);    //Port USB utilisé en mode débug
  Serial1.begin(9600);   //Port série utilisé par le XBeePro
  
  ServoAvantGauche.attach(ServoAvG);     //Attache la pin 2 au servomoteur
  ServoArrieGauche.attach(ServoArG);     //Attache la pin 3 au servomoteur
  ServoAvantDroit.attach(ServoAvD);      //Attache la pin 4 au servomoteur
  ServoArrieDroit.attach(ServoArD);      //Attache la pin 5 au servomoteur
  
  //Fixe la position au centre
  ServoAvantGauche.write(SERVO_CENTRE_AVG);
  ServoArrieGauche.write(SERVO_CENTRE_ARG);
  ServoAvantDroit.write(SERVO_CENTRE_AVD);
  ServoArrieDroit.write(SERVO_CENTRE_ARD);
  
  inputString.reserve(200);
}

/* -- LOOP -- */
void loop() {
  
  if (stringComplete) {
    // TRES MOCHE : on compte le nombre de START_CHAR pour savoir si on a pas 2 (voir plus) trame concaténée par erreur
    int firstStartChar = inputString.indexOf(START_CHAR);
    int secondStartChar = inputString.indexOf(START_CHAR, firstStartChar + 1);
    
    if(firstStartChar == 0 && secondStartChar == -1)
    {
      traitementMessage(inputString);
    } 
    
    // clear the string:
    inputString = "";
    stringComplete = false;
  }
}

void serialEvent() {
  
  while (Serial.available()) {
    
    // get the new byte:
    char inChar = (char)Serial.read();
    // add it to the inputString:
    inputString += inChar;
    
    // if the incoming character is a newline, set a flag
    // so the main loop can do something about it:
    if (inChar == STOP_CHAR) {
      stringComplete = true;
    }
    Serial.flush();  //Nettoyage de buffer
  }
}


void serialEvent1() {
  
  while (Serial1.available()) {
    
    // get the new byte:
    char inChar = (char)Serial1.read();
    // add it to the inputString:
    inputString += inChar;
    
    // if the incoming character is a newline, set a flag
    // so the main loop can do something about it:
    if (inChar == STOP_CHAR) {
      stringComplete = true;
    }
    Serial1.flush();  //Nettoyage de buffer
  }
}

void traitementMessage(String message)
{
  Serial.println(message);
  String data;
  int instruction = 0;
  int data1 = 0, data2 = 0, data3 = 0, data4 = 0, data5 = 0, data6 = 0, data7 = 0, data8 = 0, data9 = 0; 
  int index = 0, index2 = 0;
  
  int positionServoAvG = SERVO_CENTRE_AVG;
  int positionServoArG = SERVO_CENTRE_ARG;
  int positionServoAvD = SERVO_CENTRE_AVD;
  int positionServoArD = SERVO_CENTRE_ARD;
  
  // On récupère l'instruction
  index   = message.indexOf(SEP_CHAR);
  index2  = message.indexOf(SEP_CHAR, index +1);
  data    = message.substring(index +1 , index2);
  message = message.substring(index2 +1 );
  
  instruction = data.toInt();
  
  switch (instruction)
  {
    case INSTRUCTION_MOTEURS :
      for(int i = 0; i < 9; i++)
      {
        index = message.indexOf(SEP_CHAR);
        data = message.substring(0, index);
        message = message.substring(index+1);
        
        if(i == 0) data1 = data.toInt();
        if(i == 1) data2 = data.toInt();
        if(i == 2) data3 = data.toInt();
        if(i == 3) data4 = data.toInt();        
        if(i == 4) data5 = data.toInt();
        if(i == 5) data6 = data.toInt();
        if(i == 6) data7 = data.toInt();
        if(i == 7) data8 = data.toInt();
        if(i == 8) data9 = data.toInt();   
      }
      
      MoteurAvantGauche.Action(data1, data2);
      MoteurAvantDroit.Action(data3, data4);
      MoteurArriereGauche.Action(data5, data6);
      MoteurArriereDroit.Action(data7, data8);

      //delay(1000);
      delay(data9);
      
      MoteurAvantGauche.Action(0, 0);
      MoteurAvantDroit.Action(0, 0);
      MoteurArriereGauche.Action(0, 0);
      MoteurArriereDroit.Action(0, 0);
      
      
      //Serial.println("ok");
      Serial1.println("ok");
      
      break;
  
    case INSTRUCTION_DIR :
      for(int i = 0; i < 4; i++)
      {
        index = message.indexOf(SEP_CHAR);
        data = message.substring(0, index);
        message = message.substring(index+1);
        
        if(i == 0) data1 = data.toInt();
        if(i == 1) data2 = data.toInt();
        if(i == 2) data3 = data.toInt();
        if(i == 3) data4 = data.toInt();            
      }
      
      positionServoAvG = ((data1 * SERVO_CENTRE_AVG)/90);
      positionServoArG = ((data2 * SERVO_CENTRE_ARG)/90);
      positionServoAvD = ((data3 * SERVO_CENTRE_AVD)/90);
      positionServoArD = ((data4 * SERVO_CENTRE_ARD)/90);
      
      ServoAvantGauche.write(positionServoAvG);
      ServoArrieGauche.write(positionServoArG);
      ServoAvantDroit.write(positionServoAvD);
      ServoArrieDroit.write(positionServoArD);

      Serial1.println("ok");
      
      break;
  }
}

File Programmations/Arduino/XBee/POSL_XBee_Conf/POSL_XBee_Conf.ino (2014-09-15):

/*
    CONFIGURATION DU RECSEAU

    XBee0
    ATMY9990  //Adresse source
    ATDL9991  //Adresse destination (bit de poids faible)
    ATDH0     //Adresse destination (bit de poids fort)
    ATID8756  //Identifiant du réseau
    
    XBee1
    ATMY9991  //Adresse source
    ATDL9990  //Adresse destination (bit de poids faible)
    ATDH0     //Adresse destination (bit de poids fort)
    ATID8756  //Identifiant du réseau
*/

void setup() {
  Serial.begin(9600);
  XBeeConf(0);
}

void loop() {
  delay(1000);
  Serial.print("42\n");
}

void XBeeConf (int num){
  Serial.print("+++");  //Initialisation de la configuration
  
  if(num == 0) {
    Serial.print("ATDH0\r");     //Adresse destination (bit de poids fort
    Serial.print("ATDL9991\r");  //Adresse destination (bit de poids faible)
    Serial.print("ATMY9990\r");  //Adresse source
    Serial.print("ATDID8756\r"); //Identifiant du réseau
  }
  else if(num == 1) {
    Serial.print("ATDH0\r");     //Adresse destination (bit de poids fort
    Serial.print("ATDL9990\r");  //Adresse destination (bit de poids faible)
    Serial.print("ATMY9991\r");  //Adresse source
    Serial.print("ATDID8756\r"); //Identifiant du réseau
  }
  
  Serial.print("ATCN\r");  //Sortir su mode de configuration 
}

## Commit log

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2014-08-13 Ajout d'un premier système de roue. L'intégration se fait parfaitement sur les moteurs après l'essaie d'un print.
    [Roue-Type1.fcstd, Roue-Type1.stl]
2014-08-13 Modification de l'axe pour prendre en compte un ajustement due à la conception de la roue.
    [Axe_Moteur_Roue.fcstd, Axe_Moteur_Roue.stl]
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2014-08-17 Ajout des interfaces suspension. Ajout du block de raccordement vers le U en aluminium.
    [Block_Raccordement.fcstd, Block_Raccordement.stl, Interface_Servo.fcstd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]
2014-08-21 Ajout du système de suspension. Le renvoie qui sert de pivot vers le plat en aluminium qui servira de palonier vertical. Ajout d'image contenant le montage des pièces du système de suspension.
    [Bas-Suspension.stl, Bras-Suspension.fcstd, Pivot-Renvoie.fcstd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]
2014-08-21 Destruction du stl qui était raté. Le nom n'est pas correct et son contenu non plus.
    [Bas-Suspension.stl]
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2014-08-23 Mise en place des coins servant à l'ossature. Le type 1 est un essai et il est conservé pour des besoins ultérieur. De plus il faudra modéliser les plats qui servent à créer l'ossature.
    [Coin_Type1.fcstd, Coin_Type1.stl, Coin_Type2-A.fcstd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]
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2014-08-24 Retrait des pièces achetés suite à un problème de reconnaissance des documents.
    [Bras-Suspension.fcstd, Bras-Suspension.stl]
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2014-08-24 Ajout de nouvelles pièces au niveau de la suspension. Quelques interfaces ont été ajoutés aussi.
    [Embout-Deporte.fcstd, Embout-Deporte.stl, Interface-Rotule_1.fcstd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]
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2014-08-31 Ajout d'une version 2 de la queue d'arronde. Le but étant de rapprocher les plateaux entre queue d'arronde pour moduler les besoins en fonction des équipements à installé dans l'ossature.
    [Integ-Q-Arronde_B_V2.fcstd, Integ-Q-Arronde_B_V2.stl]
2014-08-31 Ajout de la section outil. Cette section est spécifique aux outils introuvable et permettent de se tirer de mauvais pas.
    [Outil_A.fcstd, Outil_A.stl, Outil_A1.fcstd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]
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2014-09-02 Ajout d'un outil pour tarauder avec des petits tarauds M3 au pas de 0.5.
    [Toune-A-Gauche_1.fcstd, Toune-A-Gauche_1.stl]
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2014-09-07 modification du fichier plateau Arduino. L'interface servant à placer les prises vers l'extérieur à été corrigé.
    [Plateau_Arduino.fcstd, Plateau_Arduino.stl]
2014-09-07 Mise en place du système de pannier à batterie. C'est un cas spécifique qui prends en compte une nouvelle version du plateau à drivers moteurs.
    [Pannier_Batterie.fcstd, Pannier_Batterie.stl, Plateau_Drivers_T1.fcstd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]
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2014-09-08 Ajout d'un système d'attache câble sur le système de suspension. Une modification du block raccordement est nécessaire.
    [Attache-Cable.fcstd, Attache-Cable.stl, Block_Raccordement.fcstd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]
2014-09-10 Ajout d'une boite de rangement pour les vis ou tout autre petits objets.
    [Boite-Type1-A.fcstd, Boite-Type1-A.stl, Boite-Type1-B.fcstd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]
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2014-09-26 Ajout de quelques fichiers et mise à jour des document. Ajout de la netlist (incomplète).
    [$savepcb.brd, Alim.brd, Alim.sch]
2014-09-28 Modification du Circuit. En raison d'une modification future, la version en cours est incorrecte. Veuillez noter que ce commit en l'état est pour mémoire avant toute nouvelle version de PCB.
    [$savepcb.brd, Alim.brd, Alim.sch]
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2014-10-09 Ajout de la carte interface TX 5V -> RX 3.3V et adaptation entre Arduino et XBee.
    [$savepcb.brd, XBeeIface.brd, XBeeIface.sch]
2014-10-26 Ajout d'une rotule optimisé pour une reprap de type Prussa i3 en couche de 0.1mm.
    [Rotule_Type1_Prussa.fcstd, Rotule_Type1_Prussa.stl]
2014-11-21 Modification de la partie alimentation. Ajout de la partie Module Mini Alim qui est un régulateur monté pour être plugé et déplugé sur la carte mère alimentation à revoir totalement. Ce procédé perme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
    [$savepcb.brd, Alim.sch, ModuleMiniAlim.brd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]
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2014-12-14 Ajout d'une pièce venant chapeauté le pivot-axe qui à une forme différente de la version précédente. Cela permet de résoudre la casse de l'axe au ras du déport de l'axe.
    [Chapeau-pivot.fcstd, Chapeau-pivot.stl, Pivot-Axe.fcstd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]
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2014-12-15 Refonte complete du PCB à cause d'un bug de Kicad sur la génération imprimé de la carte **Attention, la version précédente, les tailles de sorties sont fausses**
    [$savepcb.brd, Alim.brd]
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2014-12-15 Modification du schéma au niveau de C3 et C5 **Mise en place de la bonne valeur**
    [Alim.sch]
2015-01-06 Mise à jour de la carte Rectification d'une erreur concernant le T2 qui est un MJD45H11G
    [$savepcb.brd, Alim.brd, Alim.sch]
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2015-01-07 Modification du PCB. Emplacement de la mini alim déporté au pas de 2.54mm
    [$savepcb.brd, Alim.brd]
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2015-01-07 Retrait d'un plan trop ancien et éronné. Il sera remplacer dans un premier temps par un synoptique
    [Rover_Plan_General.dxf]
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2015-01-14 Mise à jour du plateau type 1 et ajout du plateau alimentation V3.0.
    [Plateau_AlimV3.fcstd, Plateau_AlimV3.stl, Plateau_Type_1.fcstd]
2015-01-15 Ajout d'une nouvelle pièce d'intégration. Elle fait suite à l'ajout d'un bouton ON/OFF.
    [Integ-Sub_D9-T3.fcstd, Integ-Sub_D9-T3.stl]
2015-01-17 Modification de l'interface Roture. Elle intègre désormais un emplacement pour attacher le câble de liaison.
    [Interface-Rotule_1.fcstd, Interface-Rotule_3.fcstd, Interface-Rotule_3.stl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]
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2015-01-17 Ajout d'une nouvelle version de la queue d'arronde du rack. Il intègre une hausse de matière pour permettre d'installé une trappe directement dessus.
    [Integ-Q-Arronde_B_V3.fcstd, Integ-Q-Arronde_B_V3.stl]
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2015-05-14 Retraît mise à jour Python. Bug de mise à jour GIT
    [POSL-Rover.py]
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2015-06-18 Très très moche ! Revoir la conversion de datas issue du bouton de vitesse.
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2015-06-23 Rectification bug des boutons quand la carte est pas connecté + rectification des informations données au log en cours de pilotage.
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
